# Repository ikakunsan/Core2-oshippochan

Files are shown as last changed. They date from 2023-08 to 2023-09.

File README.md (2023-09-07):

# Core2-oshippochan

こちらの参加作品です。
https://protopedia.net/prototype/4404

スタックチャンに尻尾が生えました。

# ハードウェア - Hardware
## 概要
- サーボは3つ。水平観点用 (Pan), 上下回転用 (Tilt), 尻尾用 (Tail)
- GPIOはそれぞれ、Pan: GPIO33, Tilt: GPIO32, Tail: GPIO27 を使っています。
- 脚部のUSBコネクタからは、M5Stackとサーボに給電します。電源のみでデータは繋がっていないので、M5Stackにアクセスする場合は本体側にUSBケーブルを接続する必要があります。（本体のUSBからはサーボでの電力は供給されません。サーボの貫通電流の関係です）

## 使ったもの - Items
1. M5Stack Core2 + SD card (本体のFlashを頻繁に書き込みたくなかったので) I don't want to write internal flash frequently
2. M5Stack プロトモジュール (基板とネジ) Proto-module (Using PCB and screw only)
1. サーボ (SG-90やSG-92等。上下はSG-92が良さげ。尻尾用は音の静かなSG-90がいいかも ) Servo
1. 整流用ダイオード (1A以上、ショットキーバリアは非推奨、今回はファストリカバリー使用) Diode (more than 1A. Schottky barrier diode is not recommended due to low Vf. I used fast recovery diode)
1. USB-C メスコネクタの付いた基板。今回使ったのはこれ。 PCB with USB-C female connector
1. ピンヘッダ (ライトアングル)、2pコネクタ(XH)、電線等。 Other components such as pin header, XH connector, wire etc.
1. 自作の3Dプリントパーツ (STLの下。自分のプリンタに合わせこんだので微妙なところがあるかもしれません…。素材は、筐体はなんでもいいですが、尻尾はPETG推奨。PLAは弾力に欠けるので非推奨です。ABSは試していません) Self-made 3D print parts (I put STL files in Github. Any material will be fine for body. PLA is not recommended for tail. PETG is recommended. (PLA is easy to deform so not suitable for usage like this)
1. 釣り用ナイロン糸 (0.8号) Nylon string. Thinner one is better. I used 0.155mm string for fishing.
1. M2x6mmなべタッピングビス 1個 (尻尾取り付け用)、M2x8mmなべタッピングビス 2個 (サーボ取り付け用) Tapping screw M2x6 1pcs (to fix tail), M2x8 2pcs (to fix servo)

注1) プログラム書き込み時はUSBケーブルを2本挿すことになるので、逆流防止でダイオードを入れています。Core2で使用している電源管理IC AXP192の仕様で不明の部分が多いため、安全側に振る目的で、ダイオードはVfの大きめのものを使っています。 Information in the AXP192 datasheet is insufficient and I couldn't find max voltage, so I used a fast recovery diode, it has bigger Vf, for safe. 

注2) サーボをギリギリまで寄せてしまったので付属のネジだと頭が壁にひっかかかるため、壁側は通常のM2のタッピングビスを使う必要があります。（付属のネジを無理に使うと途中で折れることがあります…） There are no (minus) margin on one side of the bottom servos, so standard M2 screw should be used on wall side.

## 製作 - How to make
（ガレキレベルの難易度です…。誰でも作れるレベルに落とし込めていません…） It will be hard to make this because parts dimensions are optimized to my 3D printer, and no pre-wred PCB (using ) etc...

1. M5Stack プロトモジュールの基板を外して、コネクタ等のパーツを取り付けて配線。写真4のように。 Detach PCB from M5Stack proto module. Assemble and wire components (header, connector diode etc). Refer to picture 4.
1. 8~9cmのワイヤにXHコネクタを取り付け、USB-C基板にはんだ付けする。このとき、基板に穴に差し込むけれど、裏には飛び出ないように。USB-C基板をプリント基板等の非金属の耐熱性のあるものにあてがって、ワイヤを穴に挿して上側からはんだ付けすると裏に飛び出ません。 Connect USB-C and XH connector to wire
1. プロトモジュール基板にM5Stackやサーボを取り付けて（筐体なしの状態での）動作確認。 Connect M5Stack and servo to the proto module and check the functions
1. シェル固定用のアームがボディーの穴に入ってスムーズに動くのを確認。アーム側を少し削るとか穴を少し広げるとか調整が必要かもしれません。ガタ防止であまり余裕もたせていないので。 Check if the arm to fix shell can set to the body and moves smoothly. (may need to trim the arm hole)
1. 足を組み立てる。ワイヤを穴に通して、サーボの取り付けパーツをはめて、カバーをスライドさせて閉じる。(写真5) Build a foot. Set the PCB and set the parts, then slide the cover.
1. 全部のサーボを90度の位置に設定。 Set all servos to 90 degree.
1. Bodyに下向きのサーボ２個を取り付ける。下面の壁側は付属のネジは使わずに、M2x8のタッピングビスを使ってください。 Fix two bottom servos to the body. Please use M2x8 screw on wall side of two bottom servos.
1. 足からのケーブルをサーボの間から通して上に出す。
1. サーボのケーブルの余るぶんは、丸くまとめてサーボの間に突っ込む。(写真3, 4) Arrange extra servo cables as shown in the picture 3 and 4.
1. 尻尾にナイロン糸を通す。長めに切って、まずは中央部を尻尾先端で二重結び。左右両方の糸を、根本まで、尻尾の穴を通す。糸を通したら、尻尾をM2x6mmのネジで本体に固定。 Tight a center of nylon string at the end of the tail and then through the holes to the base. Fix the tail to the body with M2x6 screw.
1. 尻尾側のサーボホーンを写真3のようにカットしてサーボに取り付ける。完全に平行にならない場合は写真4の向きに斜めになるように (ホーンの回転部が中心からオフセットしているので)。 Cut the servo horn as shown in the picture 3, then connect it to the servo.
糸をホーンに縛り付ける。二重結び。たるみが出ないように左右均等にピンと張ること。(ちょっと難しい) Tight the string to the horn. Make sure the string is not loose.
1. ワイヤを2回巻き付けてから上部のサーボをアームとともに取り付ける。アームをホーンで固定。 Fix the upper servo with the arm.
1. 全部のワイヤのコネクタを基板に挿す。 Connect all cables to the PCB
1. シェルをアームに取り付ける。スペーサーを介して基板とシェルをネジ止め（プロトモジュールのネジを使用）する。ワイヤ類が動作に影響しないか確認。影響するようなら基板を外してワイヤ位置を調整して組み直し。 Attach the shell to the arm. Screw the PCB with the spacer. Check if the wires interfares with body.

# ソフトウェア - Software
## 必要なもの - Requirements
- OpenAI APIのAPI Key (最初の3ヶ月は無料。以降の利用には料金引き落とし方法の登録が必要)
- Google Text to SpeechのAPI Key (引き落とし方法の登録が必要。毎月無料枠あり)

## 手順 - Procedure
1. UIFlowのファームウェアを入れる Install UIFlow firmware
2. myconf-sample.pyにWiFi接続に必要な情報やAPI Keyを入力。ファイル名を myconf.pyに変更。Edit myconf-sample.py and rename it to myconf.py
1. Githubに上がっているファイル (ルート及びresの下のWAVファイル) をM5Stack Core2に転送して実行。 - Transfer all files, including wav file to M5Stack Core2

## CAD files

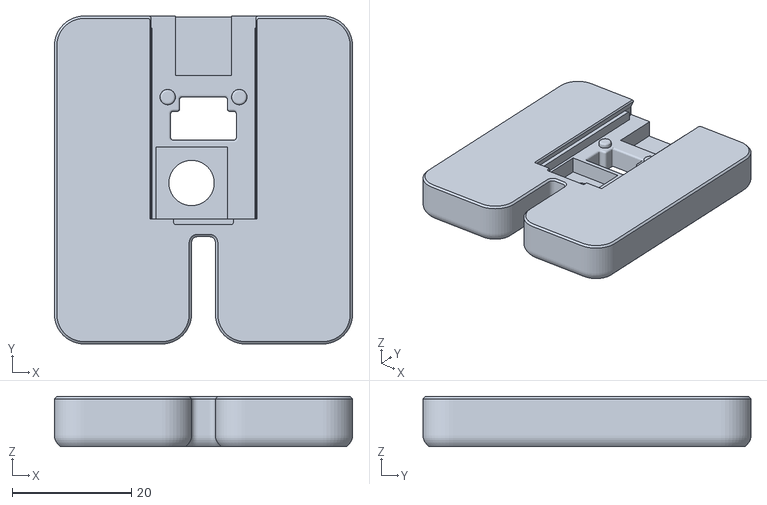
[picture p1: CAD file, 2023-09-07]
STL_files/stackchan-foot.stl
50.0 x 55.0 x 8.40

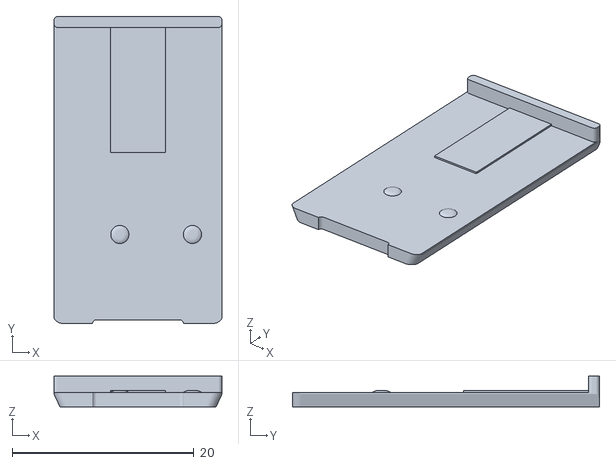
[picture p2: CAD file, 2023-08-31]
STL_files/stackchan-foot-cover.stl
18.5 x 33.8 x 3.40

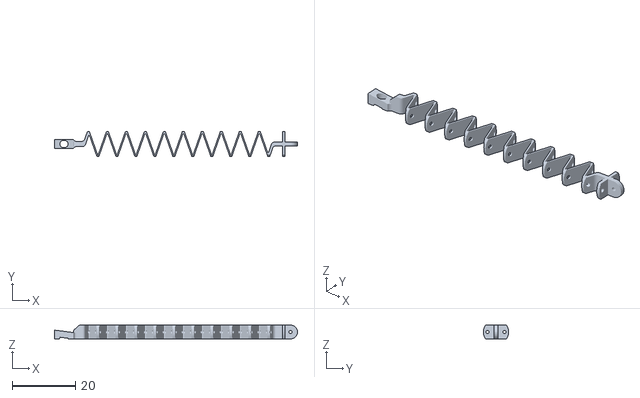
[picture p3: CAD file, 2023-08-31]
STL_files/stackchan-tail.stl
76.8 x 8.00 x 4.40

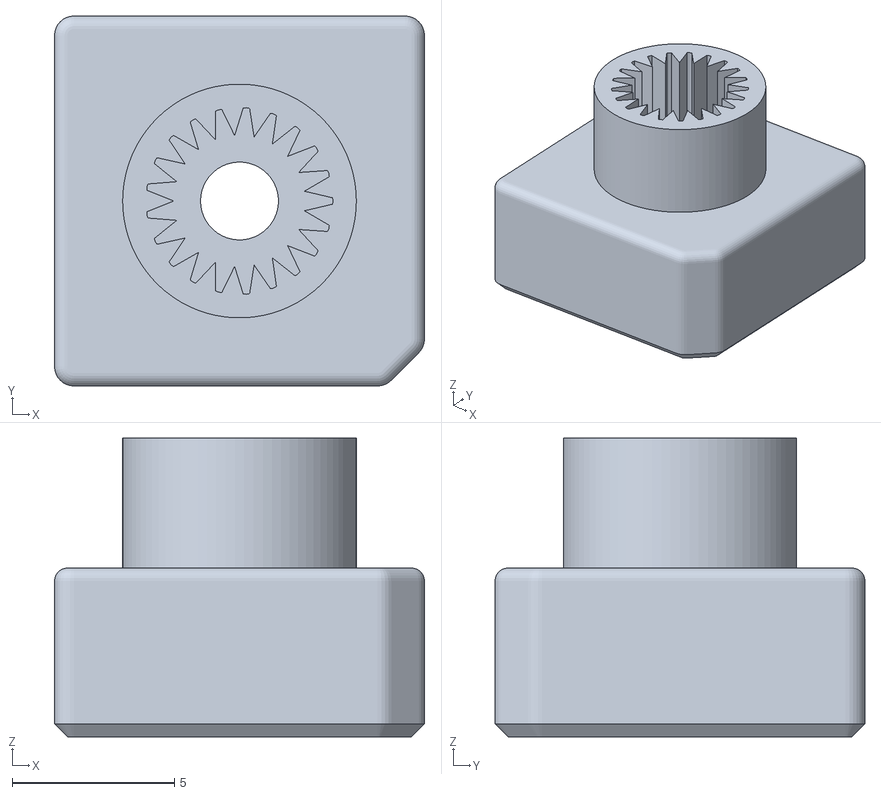
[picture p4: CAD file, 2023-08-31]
STL_files/stackchan-foot-gear.stl
11.4 x 11.4 x 9.20

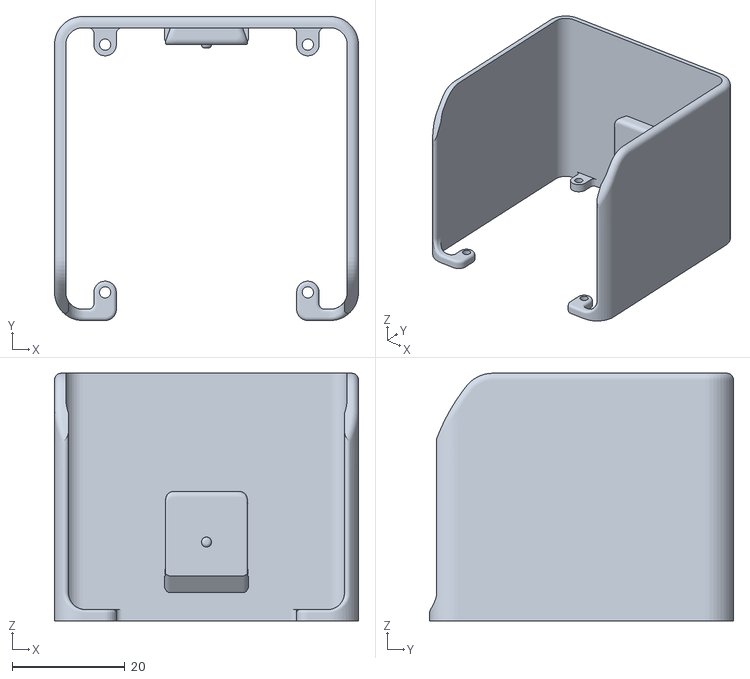
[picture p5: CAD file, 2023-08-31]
STL_files/stackchan-shell.stl
54.0 x 54.0 x 44.0

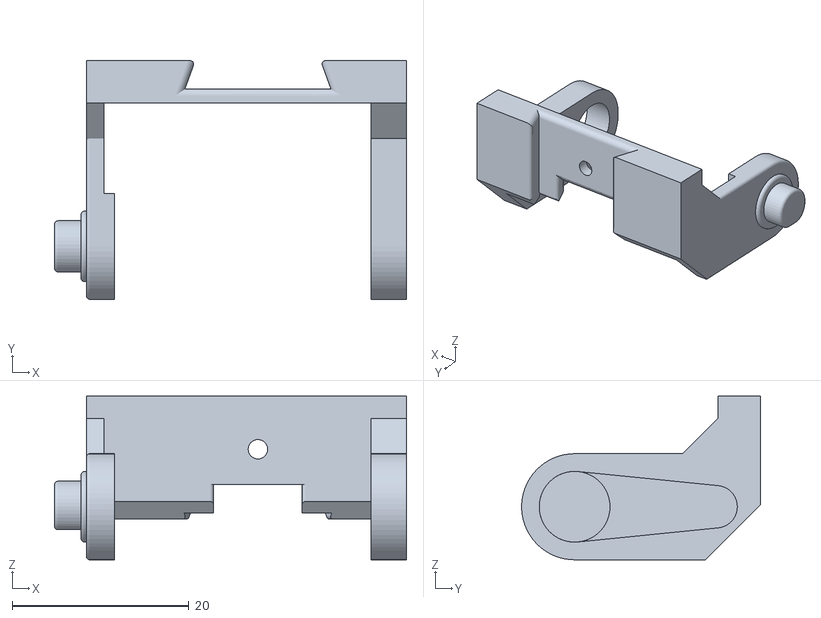
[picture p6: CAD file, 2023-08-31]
STL_files/stackchan-shell-arm.stl
39.8 x 27.0 x 18.5

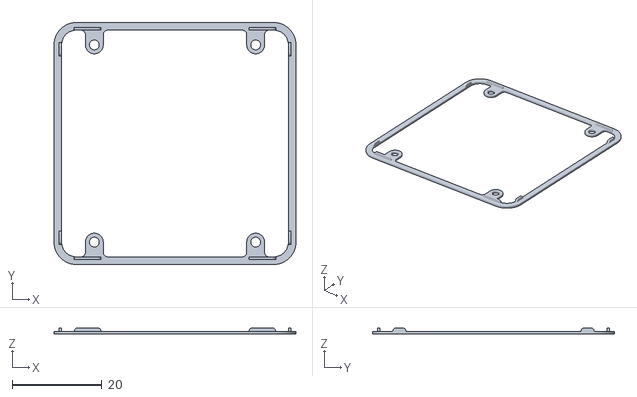
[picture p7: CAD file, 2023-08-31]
STL_files/stackchan-shell-spacer.stl
54.0 x 54.0 x 1.40

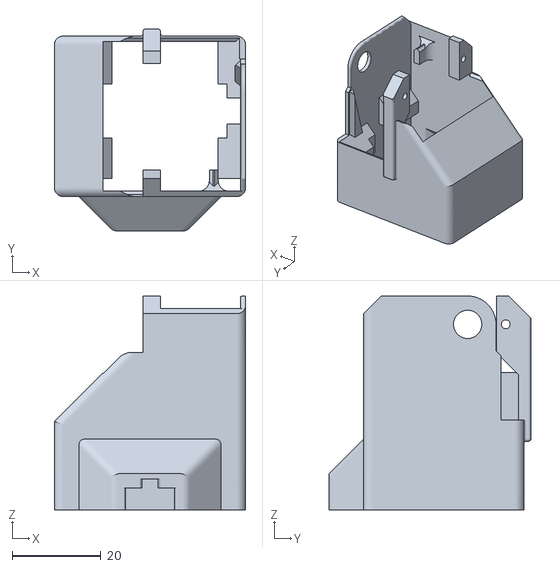
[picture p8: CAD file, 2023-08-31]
STL_files/stackchan-body.stl
43.2 x 45.6 x 48.3

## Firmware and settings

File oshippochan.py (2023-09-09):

#
# Oshippo-Chan (A variant of Stack-Chan. 変種第n号)
#

from m5stack import *
from m5stack_ui import *
from uiflow import *
from machine import Pin, PWM, Timer
import urequests as requests
import ujson
import ubinascii
import time
import random
import network
import myconf

##### ユーザーごとの設定 (ID, Password, API Keys, etc)
sta_ssid = myconf.STA_SSID  # WiFi SSID
sta_pass = myconf.STA_PASS  # WiFi パスワード
Google_API_key = myconf.Google_API_key
OpenAI_API_key = myconf.OpenAI_API_key
try:
    my_ntp_server = myconf.MY_NTP_SERVER  # time.aws.com とか使ってもよし
except:
    my_ntp_server = "time.aws.com"
#####

##### Face parts ;-) (tentative, to be updated)
eye_r = 9       # size
eyes_w = 90 / 2
eyes_y = 110
mouth_w = 40 / 2
mouth_y = 140
#####

##### Unit demendent settings
gpio_pan = 33
gpio_tilt = 32
gpio_tail = 27
offset_pan = 0  # minus for clockwise, plus for counterclockwise
offset_tilt = 0  # minus for down, plus for up
offset_tail = 0  # minus for left, plus for right
#####

##### PWM servo dependent settings
servo_cycle_ms = 20  # milisec
servo_90deg = 7.5  # テストの名残
servo_duty_min = 2.5  # 0 degree
servo_duty_max = 12.5  # 180 degree
#####

##### Servo related settings
tilt_step = 45 / 1000 * servo_cycle_ms  # degree per step
tilt_max_up = 41  # limit in degree, depends on hardware
tilt_max_down = 6  # limit in degree, depends on hardware
pan_step = 45 / 1000 * servo_cycle_ms  # degree per step
pan_max = 77  # limit in degree

pan_center = 90 + offset_pan
pan_current = 0
pan_target = pan_current
pan_actions = []
tilt_center = 80 + offset_tilt  # デフォルトは10度上向き
tilt_current = 0
tilt_target = tilt_current
tilt_actions = []

tail_center = 90 + offset_tail
tail_swing_max = 10
tail_right = True
tail_furifuri_ms = 1  # moving time in milisec
tail_pos_center = 8
tail_pos = 7.5
spf_ms = 1000
#####

##### Face related
mouth_actions = ()
mouth_mode = 0  # 0:open, 1:surprise
mouth_status = 0  # 0:not closed, 1:closed
mouth_cycle_ms = 200
#####

##### Chat GPT related
word_items = [
    "動物",
    "歴史",
    "食べ物",
    "科学",
]
#####

##### Others
pressed_button_A = False
pressed_button_B = False
pressed_button_C = False

# sound_path = "res/"
sound_path = "/sd/sound/"

idle_detection_cycle_ms = 1000
idle_detection = 15 * 60    # seconds
idle_action_cycle_ms = 1000
#idle_action_interval = 10 * 60   # seconds
idle_action_interval = 10 * 60   # seconds
idle_actions_time_next = 0      # seconds
idle_actions_time_current = 0
idle_state = True
#####


def buttonA_wasPressed():
    global tail_furifuri_ms, tail_swing_max
    global spf_ms, tail_furifuri_ms
    global tilt_target, pan_target
    global pressed_button_A

    print("*** button A was pressed")
    # lcd.print("Button A Pressed", 0, 20, 0xFFBBFF)
    # time.sleep(1)
    # lcd.print("Button A Pressed", 0, 20, lcd.BLACK)
    pressed_button_A = True


def buttonB_wasPressed():
    global tail_furifuri_ms, tail_swing_max
    global spf_ms, tail_furifuri_ms
    global tilt_target, pan_target
    global tilt_actions
    global pressed_button_B

    print("*** button B was pressed")
    # lcd.print("Button B Pressed", 0, 40, 0xFFBBFF)
    # time.sleep(1)
    # lcd.print("Button B Pressed", 0, 40, lcd.BLACK)
    pressed_button_B = True


def buttonC_wasPressed():
    global tilt_target, pan_target
    global tilt_actions
    global pressed_button_C

    print("*** button C was pressed")
    # lcd.print("Button C Pressed", 0, 60, 0xFFBBFF)
    # time.sleep(1)
    # lcd.print("Button C Pressed", 0, 60, lcd.BLACK)
    pressed_button_C = True


def buttonA_handler():
    global tail_furifuri_ms, tail_swing_max
    global spf_ms, tail_furifuri_ms
    global tilt_target, tilt_actions
    global pan_target, pan_actions
    global idle_actions_time_next

    idle_actions_time_next = time.ticks_add(idle_actions_time_next, idle_action_interval*1000)
    
    draw_eyes(0, 0, 0, lcd.WHITE, size=13)
    time.sleep_ms(300)
    draw_eyes(0, 0, 0, lcd.WHITE)
    time.sleep_ms(300)
    draw_eyes(2, 0, 0, lcd.WHITE)
    # tail_swing_max = 10
    tail_swing_max = random.uniform(8.5, 12)
    # spf_ms = 1200
    spf_ms = random.randint(800, 1200)
    tail_furifuri_ms = 6000

    pan_actions.clear()
    pan_actions = [-20, 20, 0]

    tilt_actions.clear()
    tilt_actions = [30, -15, 30, -15, 30, 0]
    do_actions()
    draw_eyes(0, 0, 0, lcd.WHITE)


def buttonB_hander():
    global tail_furifuri_ms, tail_swing_max
    global spf_ms, tail_furifuri_ms
    global tilt_target, pan_target
    global tilt_actions
    global idle_actions_time_next

    idle_actions_time_next = time.ticks_add(idle_actions_time_next, idle_action_interval*1000)
    tilt_actions.clear()
    tilt_actions = [30, -15, 30, -15, 30, 0]
    do_actions()
    pass


def buttonC_hander():
    global tail_furifuri_ms, tail_swing_max
    global spf_ms, tail_furifuri_ms
    global tilt_target, pan_target, tilt_actions
    global mouth_mode
    global idle_actions
    global idle_actions_time_next

    idle_actions_time_next = time.ticks_add(idle_actions_time_next, idle_action_interval*1000)
    
    tail_swing_max = random.uniform(8.5, 12)
    spf_ms = random.randint(800, 1200)
    tail_furifuri_ms = 4800
    mouth_mode = 0
    
    draw_eyes(0, 0, 0, lcd.WHITE, size=13)
    time.sleep_ms(300)
    draw_eyes(0, 0, 0, lcd.WHITE)

    timerSch.run("timer_Mouth", mouth_cycle_ms, 0x00)
    speaker.playWAV(sound_path + "haai.wav")
    timerSch.stop("timer_Mouth")
    
    draw_mouth(1, lcd.WHITE)
    tilt_actions.clear()
    tilt_actions = [25, -5, 0]
    do_actions()

    # call OpenAI API and Google API, and speak something

    item_num = random.randrange(len(word_items) + 1)
    if item_num < len(word_items):
        gpt_message_item = word_items[item_num]
    else:
        gpt_message_item = str(rtc.datetime()[1]) + "月" + str(rtc.datetime()[2]) + "日"

    # word_items.append(str(rtc.datetime()[1]) + "月" + str(rtc.datetime()[2]) + "日")
    # print(word_items)
    # print(random.randrange(len(word_items)))
    # print(gpt_message_item)
    gpt_message_content = gpt_message_item + "にちなんだ、うんちく話をして。60文字以内でお願い。"

    print("Sending request to OpenAI API")
    r = request_gpt(gpt_message_content)
    print(len(r))
    print("Got response from OpenAI API")
    print("Converting text data to audio file...")
    
    draw_eyes(2, 0, 0, lcd.WHITE)
    timerSch.run("timer_Mouth", mouth_cycle_ms, 0x00)
    speaker.playWAV(sound_path + "chottomatte.wav")
    timerSch.stop("timer_Mouth")
    
    draw_eyes(0, 0, 0, lcd.WHITE)
    draw_mouth(1, lcd.WHITE)
    get_wavfile(r)
    mouth_mode = 0
    timerSch.run("timer_Mouth", mouth_cycle_ms, 0x00)
    speaker.playWAV("/sd/response.wav")
    timerSch.stop("timer_Mouth")

    draw_mouth(0, lcd.WHITE)


def idle_action_handler():
    pass

def draw_eyes(style, offset_x, offset_y, color, size=eye_r):
    global eyes_w, eyes_y, eye_r

    eyesize = size
    print("drawing eyes")
    print(style, eyes_w, eyes_y, eyesize, color)
    if style == 0:  # Opened eye
        print("opened eye")
        #        eye_l_x = int(160-eyes_w+offset_x)
        eye_l_x = int(160 - eyes_w - offset_x)
        eye_r_x = int(160 + eyes_w - offset_x)
        eye_l_y = eyes_y + offset_y
        eye_r_y = eyes_y + offset_y
        lcd.rect(
            int(160 - eyes_w - 25),
            int(eyes_y - 40),
            int(eyes_w * 2 + 50),
            60,
            lcd.BLACK,
            lcd.BLACK,
        )
        #        lcd.rect(int(160-eyes_w-25), int(eyes_y-40) , int(eyes_w*2+50), 60, lcd.BLUE)
        lcd.circle(eye_l_x, eye_l_y, eyesize, color, color)
        lcd.circle(eye_r_x, eye_r_y, eyesize, color, color)
    elif style == 1:  # Closed eye
        lcd.rect(
            int(160 - eyes_w - 25),
            int(eyes_y - 40),
            int(eyes_w * 2 + 50),
            60,
            lcd.BLACK,
            lcd.BLACK,
        )
        lcd.line(int(eye_l_x - eye_r), eye_l_y, eye_l_x + eyesize, eye_l_y, color)
        lcd.line(int(eye_l_x - eye_r), eye_l_y, eye_l_x + eyesize, eye_l_y, color)
    elif style == 2:  # Puzzled eye
        lcd.rect(
            int(160 - eyes_w - 25),
            int(eyes_y - 40),
            int(eyes_w * 2 + 50),
            60,
            lcd.BLACK,
            lcd.BLACK,
        )
        lcd.line(
            int(160 - eyes_w - eye_r), int(eyes_y - eye_r), int(160 - eyes_w + eye_r), eyes_y, color
        )
        lcd.line(
            int(160 - eyes_w - eye_r), int(eyes_y + eye_r), int(160 - eyes_w + eye_r), eyes_y, color
        )
        lcd.line(
            int(160 + eyes_w + eye_r), int(eyes_y - eye_r), int(160 + eyes_w - eye_r), eyes_y, color
        )
        lcd.line(
            int(160 + eyes_w + eye_r), int(eyes_y + eye_r), int(160 + eyes_w - eye_r), eyes_y, color
        )
    elif style == 2:  # Cross eyes
        lcd.rect(
            int(160 - eyes_w - 25),
            int(eyes_y - 40),
            int(eyes_w * 2 + 50),
            60,
            lcd.BLACK,
            lcd.BLACK,
        )
        lcd.line(
            int(160 - eyes_w - eye_r), int(eyes_y - eye_r), int(160 - eyes_w + eye_r), int(eyes_y + eye_r), color
        )
        lcd.line(
            int(160 - eyes_w - eye_r), int(eyes_y + eye_r), int(160 - eyes_w + eye_r), int(eyes_y - eye_r), color
        )
        lcd.line(
            int(160 + eyes_w + eye_r), int(eyes_y - eye_r), int(160 + eyes_w - eye_r), int(eyes_y + eye_r), color
        )
        lcd.line(
            int(160 + eyes_w + eye_r), int(eyes_y + eye_r), int(160 + eyes_w - eye_r), int(eyes_y - eye_r), color
        )


def draw_mouth(style, color):  # 0:opened, 1:closeed, 2:surprised, 3:angry
    global mouth_w, mouth_y

    # print("drawing mouth ... ", end="")
    left_x = int(160 - mouth_w)
    left_y = mouth_y
    right_x = int(160 + mouth_w)
    right_y = mouth_y
    center_x = 160
    center_y = int(mouth_y + 15)
    if style == 0:  # Opened mouth
        # print("OPEN")
        #        lcd.line(left_x, left_y, right_x, right_y, lcd.BLACK)
        lcd.rect(160 - 40, mouth_y, 80, 25, lcd.BLACK, lcd.BLACK)
 #       lcd.rect(160 - 40, mouth_y, 80, 25, lcd.BLUE)
        lcd.triangle(left_x, left_y, right_x, right_y, center_x, center_y, color, color)
    elif style == 1:  # Closed mouth
        # print("CLOSE")
        #        lcd.triangle(left_x, left_y, right_x, right_y, center_x, center_y, lcd.BLACK, lcd.BLACK)
        lcd.rect(160 - 40, mouth_y, 80, 25, lcd.BLACK, lcd.BLACK)
#        lcd.rect(160 - 40, mouth_y, 80, 20, lcd.BLUE)
        lcd.line(left_x, left_y, right_x, right_y, color)
    elif style == 2:  # Surprised
        pass
    elif style == 3:  # Angry
        pass


def wink():
    # to be implemented
    pass


def random_wink():
    # to be implemented
    pass


def degree_to_pwm(degree):
    global servo_90deg, servo_duty_min, servo_duty_max

    return servo_duty_min + degree * (servo_duty_max - servo_duty_min) / 180


def wait_tilt_ms():
    global tilt_target, tilt_current, tilt_step, servo_cycle_ms

    return int(abs(tilt_target - tilt_current) / tilt_step * servo_cycle_ms +500)


def wait_pan_ms():
    global pan_target, pan_current, pan_step, servo_cycle_ms

    return int(abs(pan_target - pan_current) / pan_step * servo_cycle_ms)


def do_actions():
    global tilt_actions, pan_actions
    global tilt_target, pan_target

    for i in range(len(tilt_actions)):
        tilt_target = tilt_actions[i]
        time.sleep_ms(wait_tilt_ms())
    for i in range(len(pan_actions)):
        pan_target = pan_actions[i]
        time.sleep_ms(wait_pan_ms())
    pass


def request_gpt(input_text):
    req_url = "https://api.openai.com/v1/chat/completions"
    req_headers = {}
    #    req_headers["Authorization"] = "Bearer $(gcloud auth application-default print-access-token)"
    req_headers["Content-Type"] = "application/json"
    req_headers["Authorization"] = "Bearer " + OpenAI_API_key

    gpt_message_content = input_text

    gpt_send_data = {
        "model": "gpt-3.5-turbo",
        "messages": [
            {
                "role": "user",
                "content": gpt_message_content,
            }
        ],
        "temperature": 0.9,
        "max_tokens": 500,
    }

    req_data = ujson.dumps(gpt_send_data)
    req_data = req_data.encode()

    print("Post data")
    try:
        res = requests.post(
            url=req_url,
            headers=req_headers,
            data=req_data,
        )
        print("Get Res")

        d = ujson.loads(res.text)
        r = d["choices"][0]["message"]["content"]
        res.close()
    except:
        print("Failed to connect to OpenAI server. Maybe not connected to the Internet")
        r = ""

    return r


def get_wavfile(input_text):
    req_url = "https://texttospeech.googleapis.com/v1beta1/text:synthesize"
    req_url = req_url + "?key=" + Google_API_key
    req_headers = {}
    req_headers["Content-Type"] = "application/json; charset=utf-8"
    req_headers["X-goog-api-key"] = Google_API_key
    # req_data内のパラメータ変更はお好みで（参考リンク）：
    # https://cloud.google.com/text-to-speech/docs/reference/rest/v1beta1/AudioConfig
    # https://cloud.google.com/text-to-speech/docs/voices?hl=ja
    req_data = {
        "input": {"text": ""},
        "voice": {
            "languageCode": "ja-jp",
            "name": "ja-JP-Neural2-B",
            "ssmlGender": "FEMALE",
        },
        "audioConfig": {"audioEncoding": "LINEAR16", "speakingRate": 1.1, "pitch": 2},
    }

    req_data["input"]["text"] = input_text

    req_data = ujson.dumps(req_data)
    req_data = req_data.encode()

    print("Posting info to Google Cloud")
    res = requests.post(
        url=req_url,
        headers=req_headers,
        data=req_data,
    )
    print(res.status_code)
    print(res.reason)

    b64 = res.text[20:-202]

    # # ujosnで処理すると超遅い・・・
    # print("Converting json to dict")
    # res_dict = ujson.loads(res.text)
    # print("Picking base64 part")
    # b64 = res_dict["audioContent"]
    
    print(len(res.text))

    print("Decoding base64")
    wav = ubinascii.a2b_base64(b64)
    print("Start file writing")
    #    with open("res/response.wav", "bw") as f:
    with open("/sd/response.wav", "bw") as f:
        f.write(wav)
    print("End file writing")

    res.close()


def junbi_taiso():
    global tail_furifuri_ms, tail_swing_max
    global spf_ms, tail_furifuri_ms
    global tilt_target, pan_target

    # 電源投入後の準備運動 B-)
    pan_target = 30
    time.sleep_ms(wait_pan_ms())
    pan_target = -30
    time.sleep_ms(wait_pan_ms())
    pan_target = 0
    time.sleep_ms(wait_pan_ms())
    tilt_target = 30
    time.sleep_ms(wait_tilt_ms())
    tilt_target = -5
    time.sleep_ms(wait_tilt_ms())
    tilt_target = 0
    time.sleep_ms(wait_tilt_ms())
    time.sleep(1)


########## Timer Events

# 駆動系
@timerSch.event("timer_Servo")
def ttimer_Servo():
    # def servo_move(timer):
    global tail_furifuri_ms
    global tail_pos
    global tail_right
    global tail_swing_max, servo_90deg, offset_tail
    global tilt_center, tilt_current, tilt_target, tilt_step
    global tilt_max_up, tilt_max_down
    global pan_center, pan_current, pan_target, pan_step
    global pan_max

    ##### Tail
    tail_swing_width = tail_swing_max - servo_90deg + offset_tail
    if tail_furifuri_ms > 0:
        tail_furifuri_ms -= servo_cycle_ms
        if tail_right == True:
            tail_pos += tail_swing_width * 4 / spf_ms * servo_cycle_ms
            pwm_tail.duty(tail_pos)
            if tail_pos >= tail_pos_center + tail_swing_width:
                tail_right = False
        else:
            tail_pos -= tail_swing_width * 4 / spf_ms * servo_cycle_ms
            pwm_tail.duty(tail_pos)
            if tail_pos <= tail_pos_center - tail_swing_width:
                tail_right = True
    #    print(tail_furifuri_ms, tail_pos)

    ##### Tilt
    if tilt_current < tilt_target:
        tilt_current += tilt_step
    elif tilt_current > tilt_target:
        tilt_current -= tilt_step
    if abs(tilt_target - tilt_current) < tilt_step:
        tilt_current = tilt_target
    angle_current = tilt_center - tilt_current
    #    print(tilt_center-tilt_target, angle_current, tilt_current)
    pwm_tilt.duty(degree_to_pwm(angle_current))

    ##### Pan
    if pan_current < pan_target:
        pan_current += pan_step
    elif pan_current > pan_target:
        pan_current -= pan_step
    if abs(pan_target - pan_current) < pan_step:
        pan_current = pan_target
    angle_current = pan_center + pan_current

    #    print(pan_center+pan_target, angle_current, pan_current)
    pwm_pan.duty(degree_to_pwm(angle_current))

### 目
# @timerSch.event("timer_Eyes")
# def ttimer_Eyes():
#    pass

### 口
@timerSch.event("timer_Mouth")
def ttimer_Mouth():
    global mouth_actions, mouth_mode, mouth_status

    if mouth_status == 0:
        draw_mouth(mouth_mode, lcd.WHITE)
        mouth_status = 1
    else:
        draw_mouth(1, lcd.WHITE)
        mouth_status = 0


# アイドル検出
@timerSch.event("timer_IdleCheck")
def ttimer_IdleCheck():
    global idle_action_interval, idle_actions_time_next
    global tail_swing_max, tail_furifuri_ms, spf_ms
    


# アイドル時のランダムな動き
@timerSch.event("timer_IdleAction")
def ttimer_IdleAction():
    global idle_action_interval, idle_actions_time_next
    global tail_swing_max, tail_furifuri_ms, spf_ms
    
    if time.ticks_diff(time.ticks_ms(), idle_actions_time_next) >= 0:
        print("### idle event")
        tail_swing_max = random.uniform(8.5, 12)
        spf_ms = random.randint(1200, 2000)
        tail_furifuri_ms = random.randint(1800, 3500)
        time.sleep_ms(4000)
        idle_actions_time_next = time.ticks_add(time.ticks_ms(), idle_action_interval*1000)


################################# Main
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

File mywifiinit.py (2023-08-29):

# wifi initial settings
#
#   This assumes a file named "myconf.py", that contains below lines;
#     STA_SSID = "your WiFi SSID name"
#     STA_PASS = "your WiFi password"
#
import network
import myconf

sta_ssid = myconf.STA_SSID
sta_pass = myconf.STA_PASS
# ap_ssid = myconf.AP_SSID      # In case of activating AP
# ap_pass = myconf.AP_PASS      # In case of activating AP

def wifiinit():
    wlan = network.WLAN(network.STA_IF)
    wlan.active(True)
    wlan.connect(sta_ssid, sta_pass)
    ap = network.WLAN(network.AP_IF)
    ap.active(False)

    # ap.active(True)
    # ap.config(essid=ap_ssid, password=ap_pass, hidden=True)
    # ap.config(max_clients=10)

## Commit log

2023-08-31 Some updates
    [stackchan-body.stl, stackchan-foot-cover.stl, stackchan-foot-gear.stl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]
2023-08-31 Update STL files
    [stackchan-foot-cover.stl, stackchan-foot.stl]
2023-09-07 Update for release
    [stackchan-foot.stl]
